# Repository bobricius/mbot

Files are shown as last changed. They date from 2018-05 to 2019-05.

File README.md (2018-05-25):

# mbot

2D actuator move micro robot in X/Y 2D space
Less than 10$ educational platform with micro magnetic robot (mBot), 
only 6 GPIO to move in unlimited X/Y 2D space

Great for physical education for languages like Karel and make 
SKOBAN game or solve acrylic cutted labyrinth. 

My project not violating SRI international patent 
(maybe, I am not patent expert) 

There is differences: 

- I am using another moving track configutation 
- Control is 3-phase unipolar against 4-phase bipolar 
- My manipulator (mBot) use 4 magnets and not levitating 
- For move in one dimension I need only 3x Mosfets connected to any MCU 
(Arduino Atmega328, Stm32, MSP430, ESP XXXX) 
- 6 GPIO to move in X/Y 2D space 
- Moving board can be produced in any fab, it is just only PCB board 8/8mil 
- IT IS CHEAP

PROJECT PAGE

https://hackaday.io/project/154496-2d-actuator-move-micro-robot-in-xy-2d-space

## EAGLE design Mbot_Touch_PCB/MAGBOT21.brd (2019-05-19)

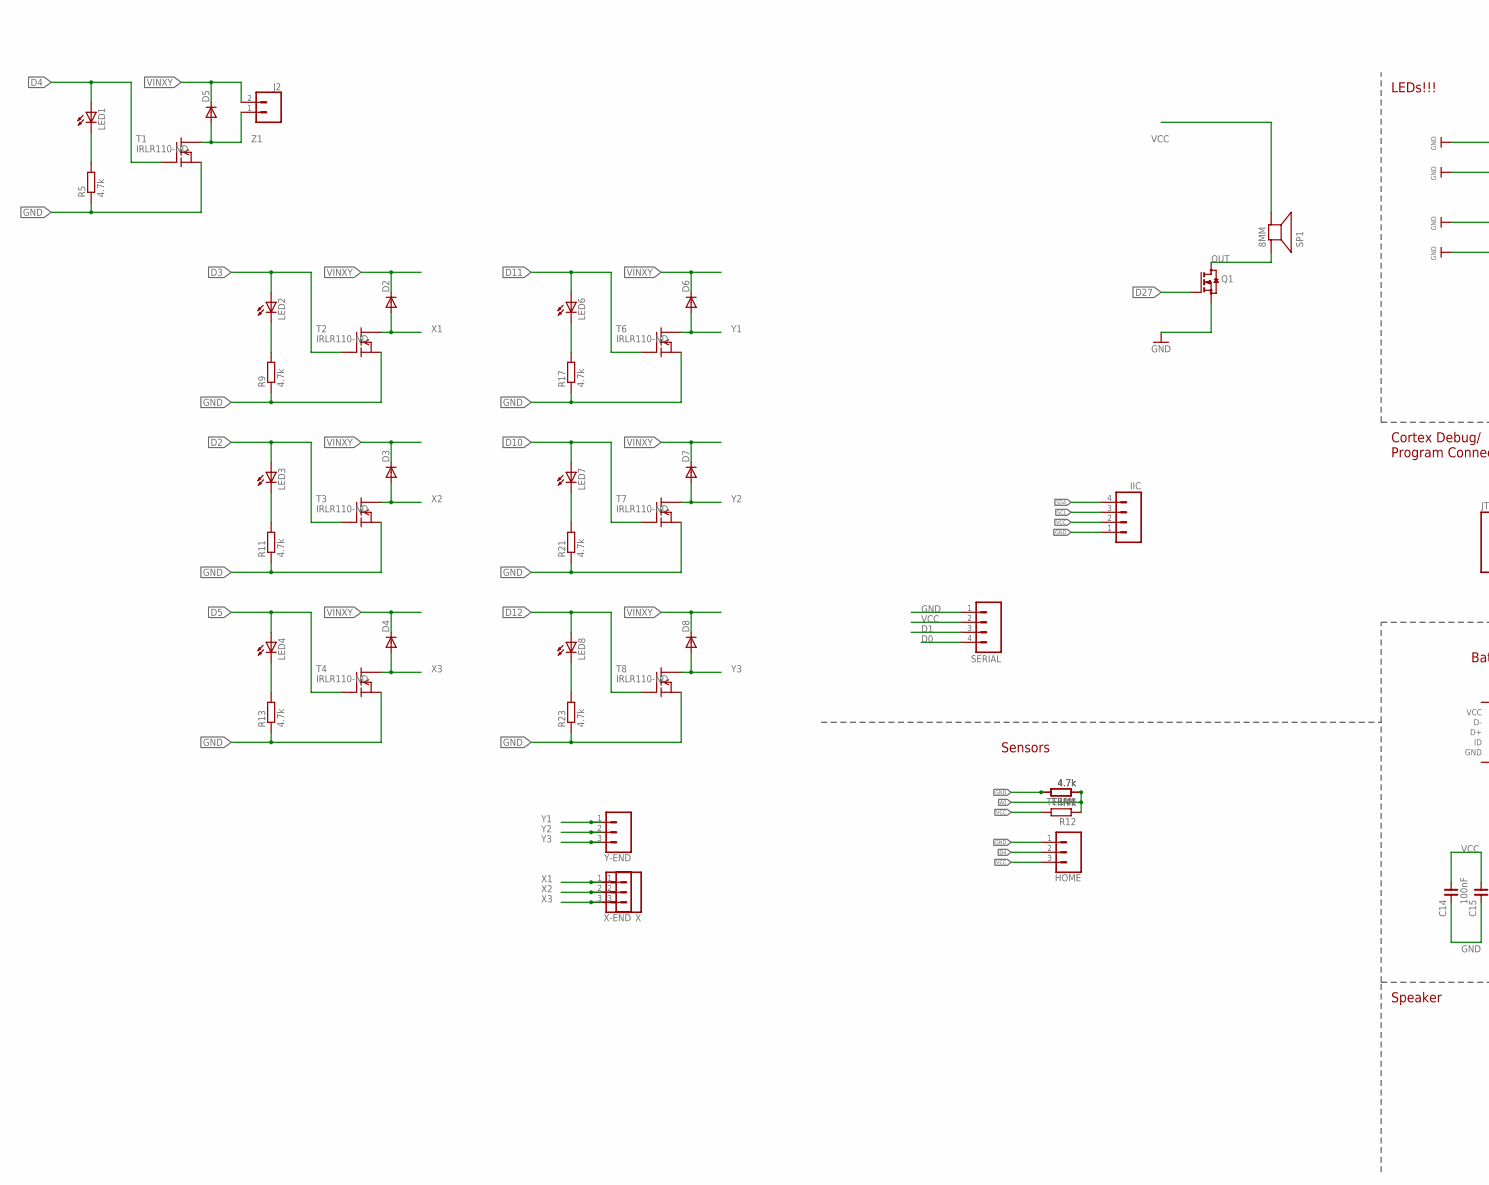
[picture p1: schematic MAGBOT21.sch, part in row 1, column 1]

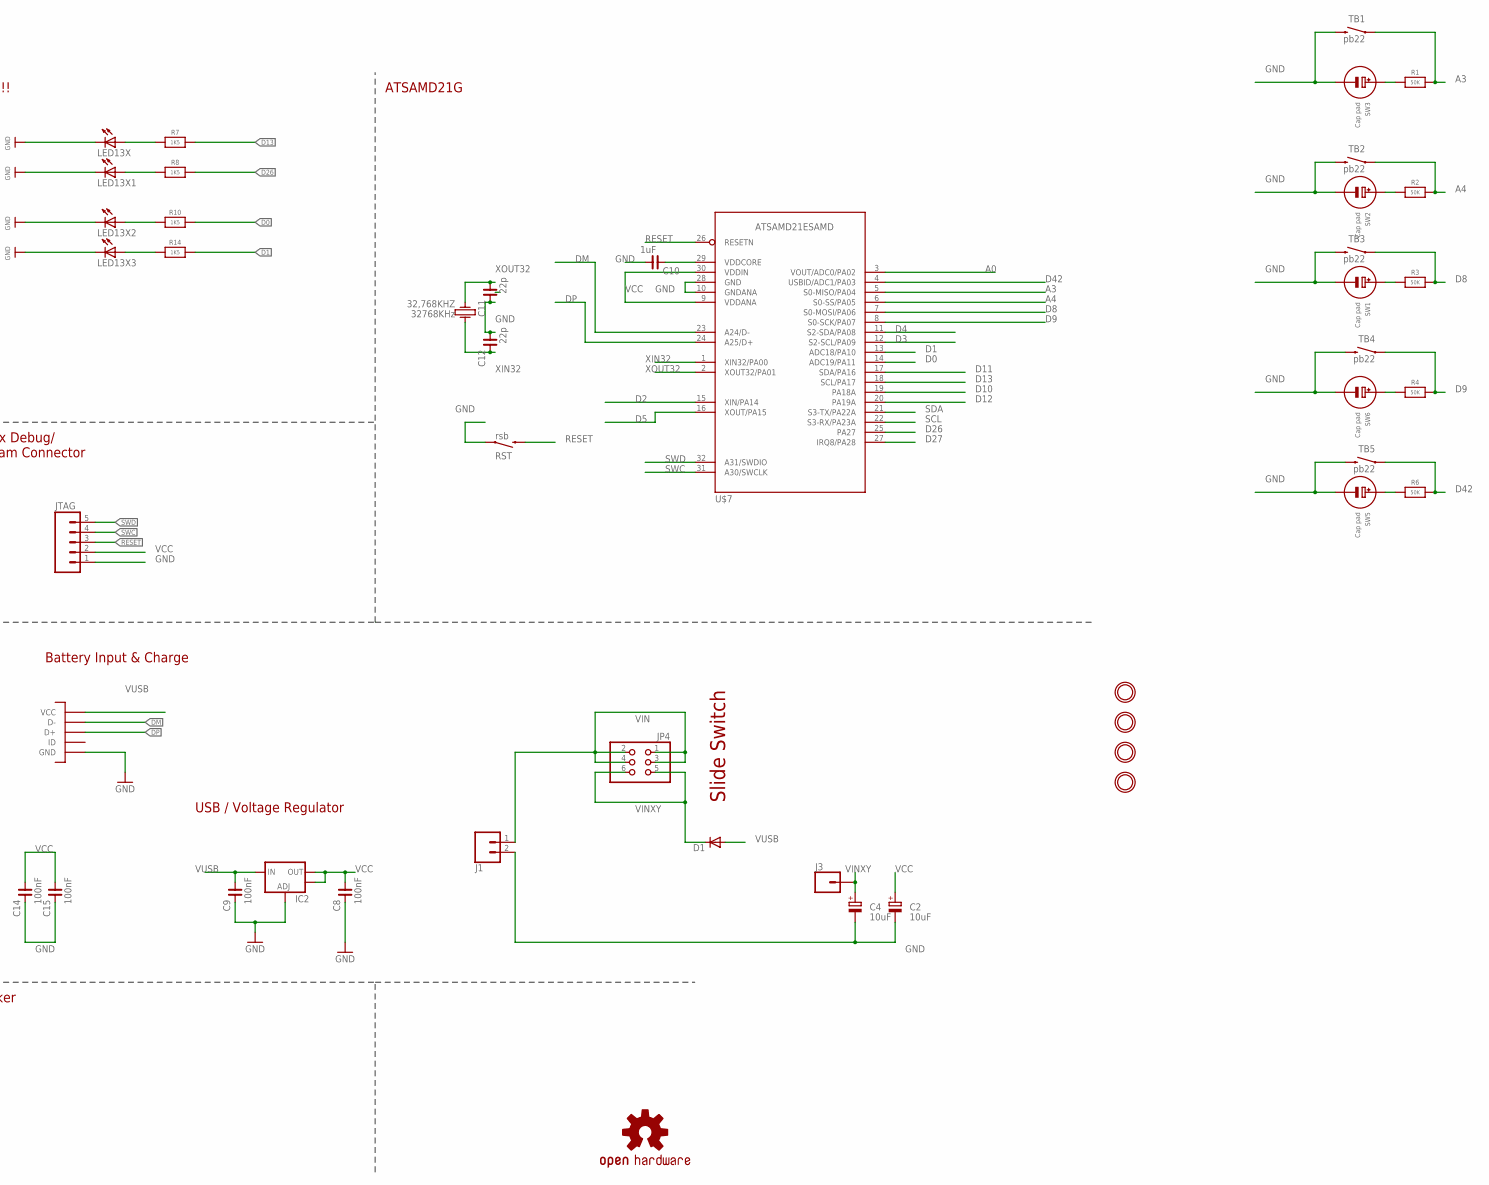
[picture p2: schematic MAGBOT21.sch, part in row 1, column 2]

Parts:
32,768KHZ: 32768KHz; KX-327LT
C2, C4: 10uF; 153CLV-0605
C8, C9: 100nF; C0603
C10: 1uF; C0805
C11, C12: 22p; C0805
C14, C15: 100nF; C0805
D1, D2, D3, D4, D5, D6, D7, D8: DIODE-DO214AC; DO214AC
HOME: CONN_031X03_NO_SILK; 1X03_NO_SILK
IC2: V_REG_LM1117SOT223; SOT223
IIC: M041X04_NO_SILK; 1X04_NO_SILK
J1, J2: CONN_02PTH3; 1X02_LONGPADS
J3: CONN_01PTH_NO_SILK_KIT; 1X01NS_KIT
JP4: PINHD-2X3; 2X03
JTAG: M051.27MM; 1X05-1.27MM
LED1, LED2, LED3, LED4, LED6, LED7, LED8, LED13X, LED13X1: LEDCHIPLED_0805; CHIPLED_0805
LED13X2, LED13X3: LEDCHIPLED_0603; CHIPLED_0603
LOGO3: OSHW-LOGOS; OSHW-LOGO-S
Q1: BSS123; SOT23
R1, R2, R3, R4, R6: 50K; _0805
R5, R9, R11, R12, R13, R17, R21, R23: 4.7k; R0603
R7: 1K5; _0805MP
R8: 1K5; 0603-NO
R10, R14: 1K5; _0603MP
RST: rsb; TACTILE_SWITCH_SMD-3
SERIAL: M041X04_NO_SILK; 1X04_NO_SILK
SP1: 8MM; BUZZER_SMT_5MM
SW1, SW2, SW3, SW5, SW6: Cap pad; CAPTOUCH_SIMPLE_12.5MM
T1, T2, T3, T4, T6, T7, T8: IRLR110-ND; TO252
TB1, TB2, TB3, TB4, TB5: pb22; TACTILE_SWITCH_SMD-3
TERM, TERM1: 4.7k; R0805W
U$3, U$4, U$8, U$10: MOUNTINGHOLE2.0; MOUNTINGHOLE_2.0_PLATED
U$5: MICROUSB; MICRO_B
U$7: ATSAMD21ESAMD; TQFP32-08
X: CONN_031X03_NO_SILK; 1X03_NO_SILK
X-END: CONN_031X03_NO_SILK; 1X03_NO_SILK
Y-END: CONN_031X03_NO_SILK; 1X03_NO_SILK

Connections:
A0: R12.1, TERM.1, TERM1.1, U$7.3 (VOUT/ADC0/PA02)
A3: R1.1, TB1.1, U$7.5 (S0-MISO/PA04)
A4: R2.1, TB2.1, U$7.6 (S0-SS/PA05)
D0: R10.1, SERIAL.4, U$7.14 (ADC19/PA11)
D1: R14.1, SERIAL.3, U$7.13 (ADC18/PA10)
D2: LED3.A, T3.1 (G), U$7.15 (XIN/PA14)
D3: LED2.A, T2.1 (G), U$7.12 (S2-SCL/PA09)
D4: HOME.2, LED1.A, T1.1 (G), U$7.11 (S2-SDA/PA08)
D5: LED4.A, T4.1 (G), U$7.16 (XOUT/PA15)
D8: R3.1, TB3.1, U$7.7 (S0-MOSI/PA06)
D9: R4.1, TB4.1, U$7.8 (S0-SCK/PA07)
D10: LED7.A, T7.1 (G), U$7.19 (PA18A)
D11: LED6.A, T6.1 (G), U$7.17 (SDA/PA16)
D12: LED8.A, T8.1 (G), U$7.20 (PA19A)
D13: R7.1, U$7.18 (SCL/PA17)
D26: R8.1, U$7.25 (PA27)
D27: Q1.1 (G), U$7.27 (IRQ8/PA28)
D42: R6.1, TB5.1, U$7.4 (USBID/ADC1/PA03)
DM: U$5.P2 (D-), U$7.23 (A24/D-)
DP: U$5.P3 (D+), U$7.24 (A25/D+)
GND: C2.-, C4.-, C8.2, C9.2, C10.1, C11.2, C12.1, C14.2, C15.2, HOME.1, IC2.1 (ADJ), IIC.1, J1.2, JTAG.1, LED13X.C, LED13X1.C, LED13X2.C, LED13X3.C, Q1.2 (S), R5.1, R9.1, R11.1, R13.1, R17.1, R21.1, R23.1, RST.1, SERIAL.1, SW1.G (-), SW2.G (-), SW3.G (-), SW5.G (-), SW6.G (-), T1.2 (S), T2.2 (S), T3.2 (S), T4.2 (S), T6.2 (S), T7.2 (S), T8.2 (S), TB1.4 (2), TB2.4 (2), TB3.4 (2), TB4.4 (2), TB5.4 (2), TERM.2, TERM1.2, U$5.GND1 (GND), U$5.GND2 (GND), U$5.GND3 (GND), U$5.GND4 (GND), U$5.GND7 (GND), U$5.GND8 (GND), U$5.P5 (GND), U$7.10 (GNDANA), U$7.28 (GND)
unnamed: R6.2, SW5.E (+)
unnamed: R4.2, SW6.E (+)
unnamed: R3.2, SW1.E (+)
unnamed: R2.2, SW2.E (+)
unnamed: R1.2, SW3.E (+)
unnamed: LED13X1.A, R8.2
unnamed: LED2.C, R9.2
unnamed: LED6.C, R17.2
unnamed: C10.2, U$7.29 (VDDCORE)
unnamed: LED3.C, R11.2
unnamed: LED7.C, R21.2
unnamed: LED4.C, R13.2
unnamed: LED8.C, R23.2
unnamed: LED13X.A, R7.2
unnamed: LED1.C, R5.2
unnamed: LED13X2.A, R10.2
unnamed: LED13X3.A, R14.2
OUT: Q1.3 (D), SP1.+
RESET: JTAG.3, RST.4 (2), U$7.26 (RESETN)
SCL: IIC.3, U$7.22 (S3-RX/PA23A)
SDA: IIC.4, U$7.21 (S3-TX/PA22A)
SWC: JTAG.4, U$7.31 (A30/SWCLK)
SWD: JTAG.5, U$7.32 (A31/SWDIO)
VCC: C2.+, C8.1, C14.1, C15.1, HOME.3, IC2.2 (OUT), IC2.4 (OUT), IIC.2, JTAG.2, R12.2, SERIAL.2, SP1.-, U$7.9 (VDDANA), U$7.30 (VDDIN)
VIN: J1.1, JP4.1, JP4.2, JP4.3, JP4.4
VINXY: C4.+, D1.C, D2.C, D3.C, D4.C, D5.C, D6.C, D7.C, D8.C, J2.2, J3.1, JP4.5, JP4.6
VUSB: C9.1, D1.A, IC2.3 (IN), U$5.P1 (VCC)
X1: D2.A, T2.3 (D), X.1, X-END.1
X2: D3.A, T3.3 (D), X.2, X-END.2
X3: D4.A, T4.3 (D), X.3, X-END.3
XIN32: 32,768KHZ.1, C12.2, U$7.1 (XIN32/PA00)
XOUT32: 32,768KHZ.4, C11.1, U$7.2 (XOUT32/PA01)
Y1: D6.A, T6.3 (D), Y-END.1
Y2: D7.A, T7.3 (D), Y-END.2
Y3: D8.A, T8.3 (D), Y-END.3
Z1: D5.A, J2.1, T1.3 (D)

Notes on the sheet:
USB / Voltage Regulator
LEDs!!!
Cortex Debug/ Program Connector
Sensors
ATSAMD21G
Battery Input & Charge
Speaker
Slide Switch

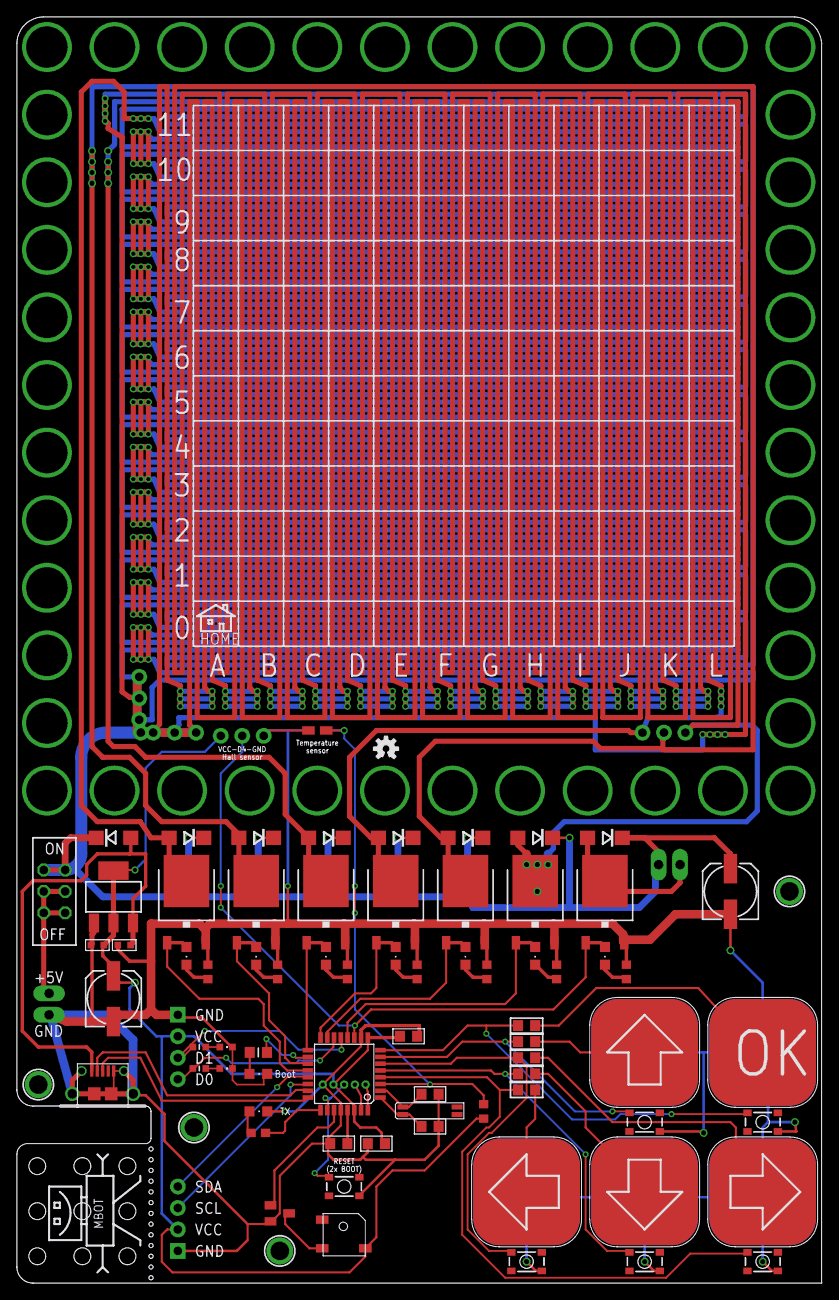
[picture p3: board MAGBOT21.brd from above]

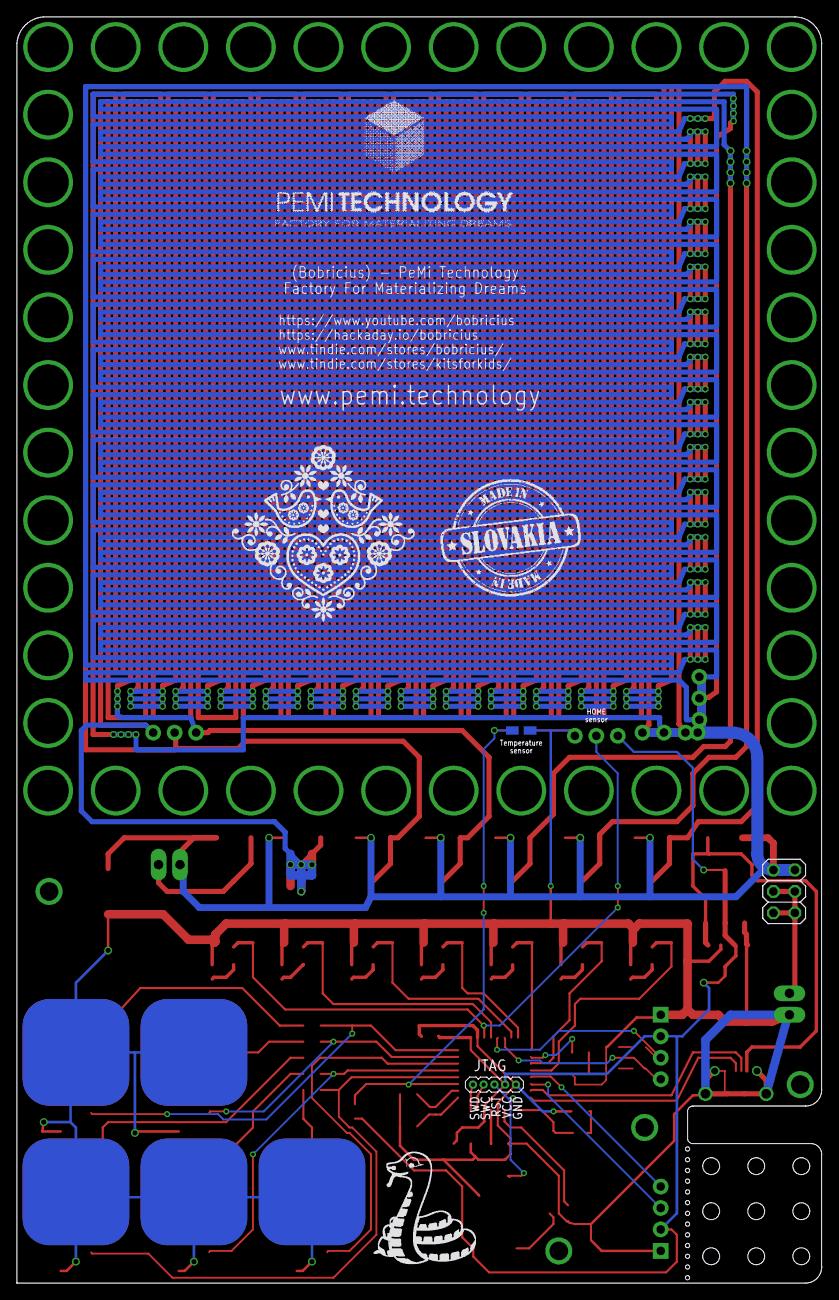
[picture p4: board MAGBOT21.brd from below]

Board: 2 copper layers, 95.2 x 149.9 mm, 87 parts (4 on the bottom side), 57 nets.

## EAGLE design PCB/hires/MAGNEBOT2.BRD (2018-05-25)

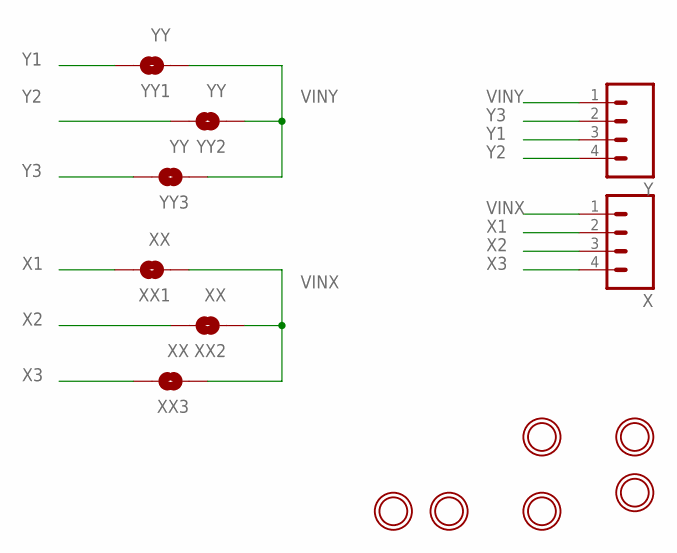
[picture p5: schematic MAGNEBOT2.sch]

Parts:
U$1, U$2, U$3, U$4, U$5, U$10: MOUNTINGHOLE2.0; MOUNTINGHOLE_2.0_PLATED
X: M04PTH; 1X04
XX1, XX2, XX3: XX; SJ_2S-TRACE
Y: M04PTH; 1X04
YY1, YY2, YY3: YY; SJ_2S-TRACE

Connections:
VINX: X.1, XX1.1, XX2.1, XX3.1
VINY: Y.1, YY1.1, YY2.1, YY3.1
X1: X.2, XX1.2
X2: X.3, XX2.2
X3: X.4, XX3.2
Y1: Y.3, YY1.2
Y2: Y.4, YY2.2
Y3: Y.2, YY3.2

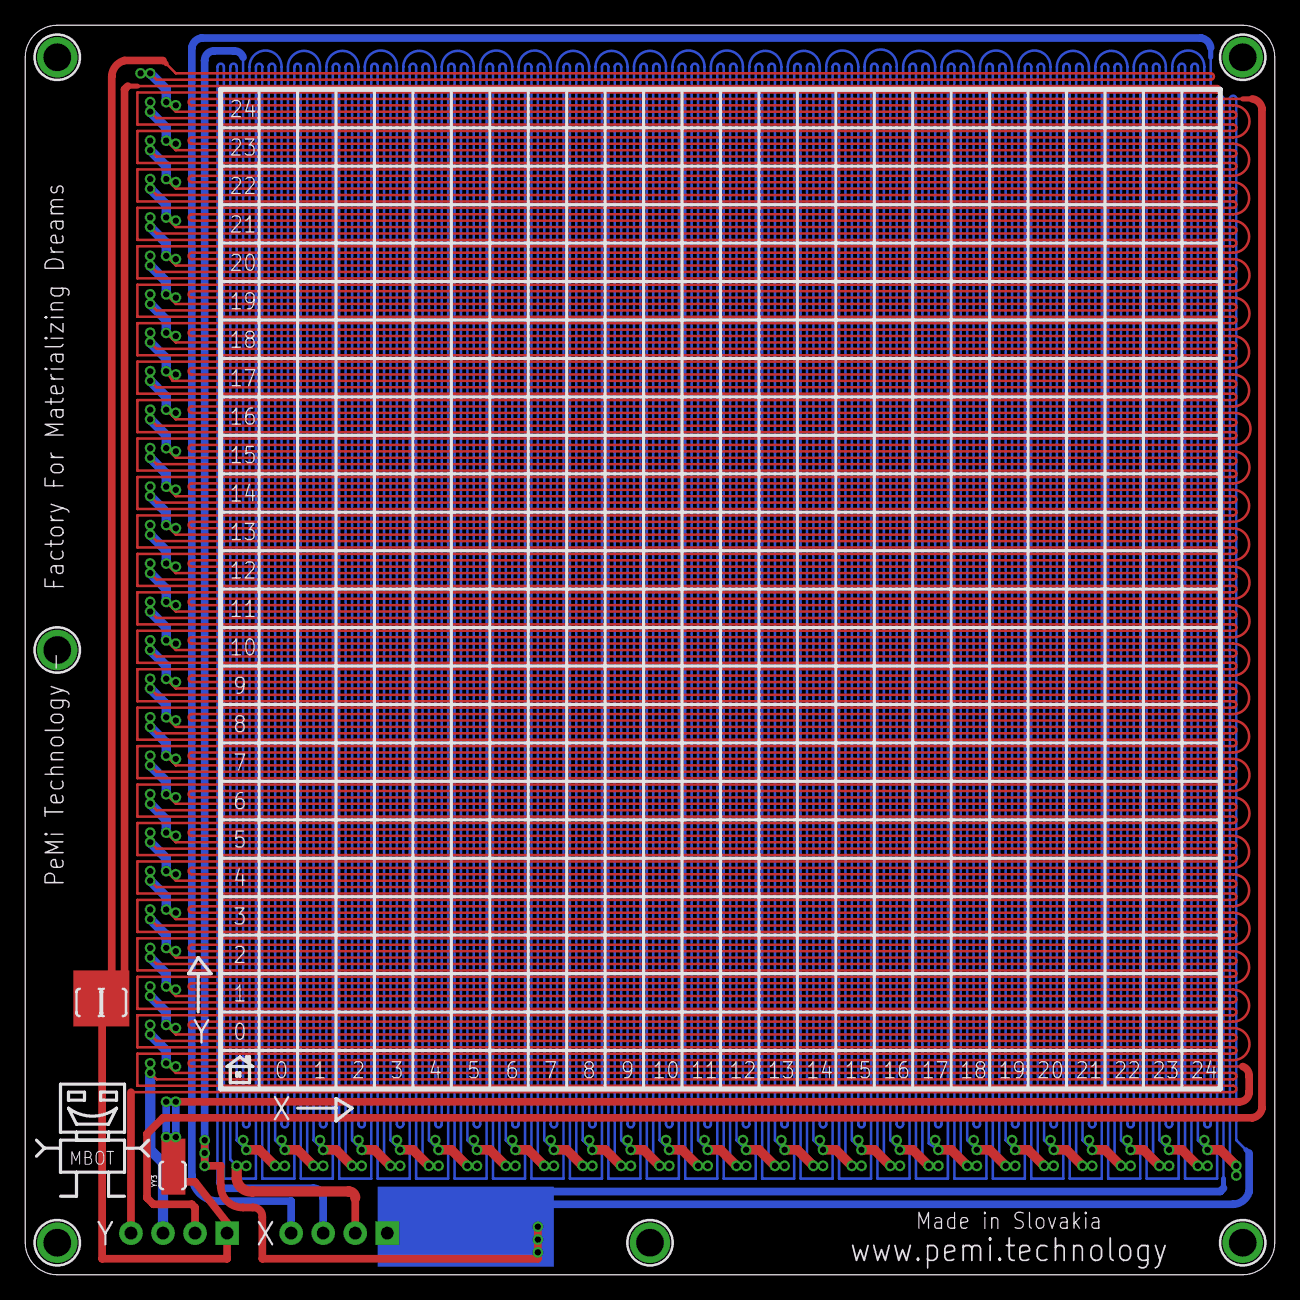
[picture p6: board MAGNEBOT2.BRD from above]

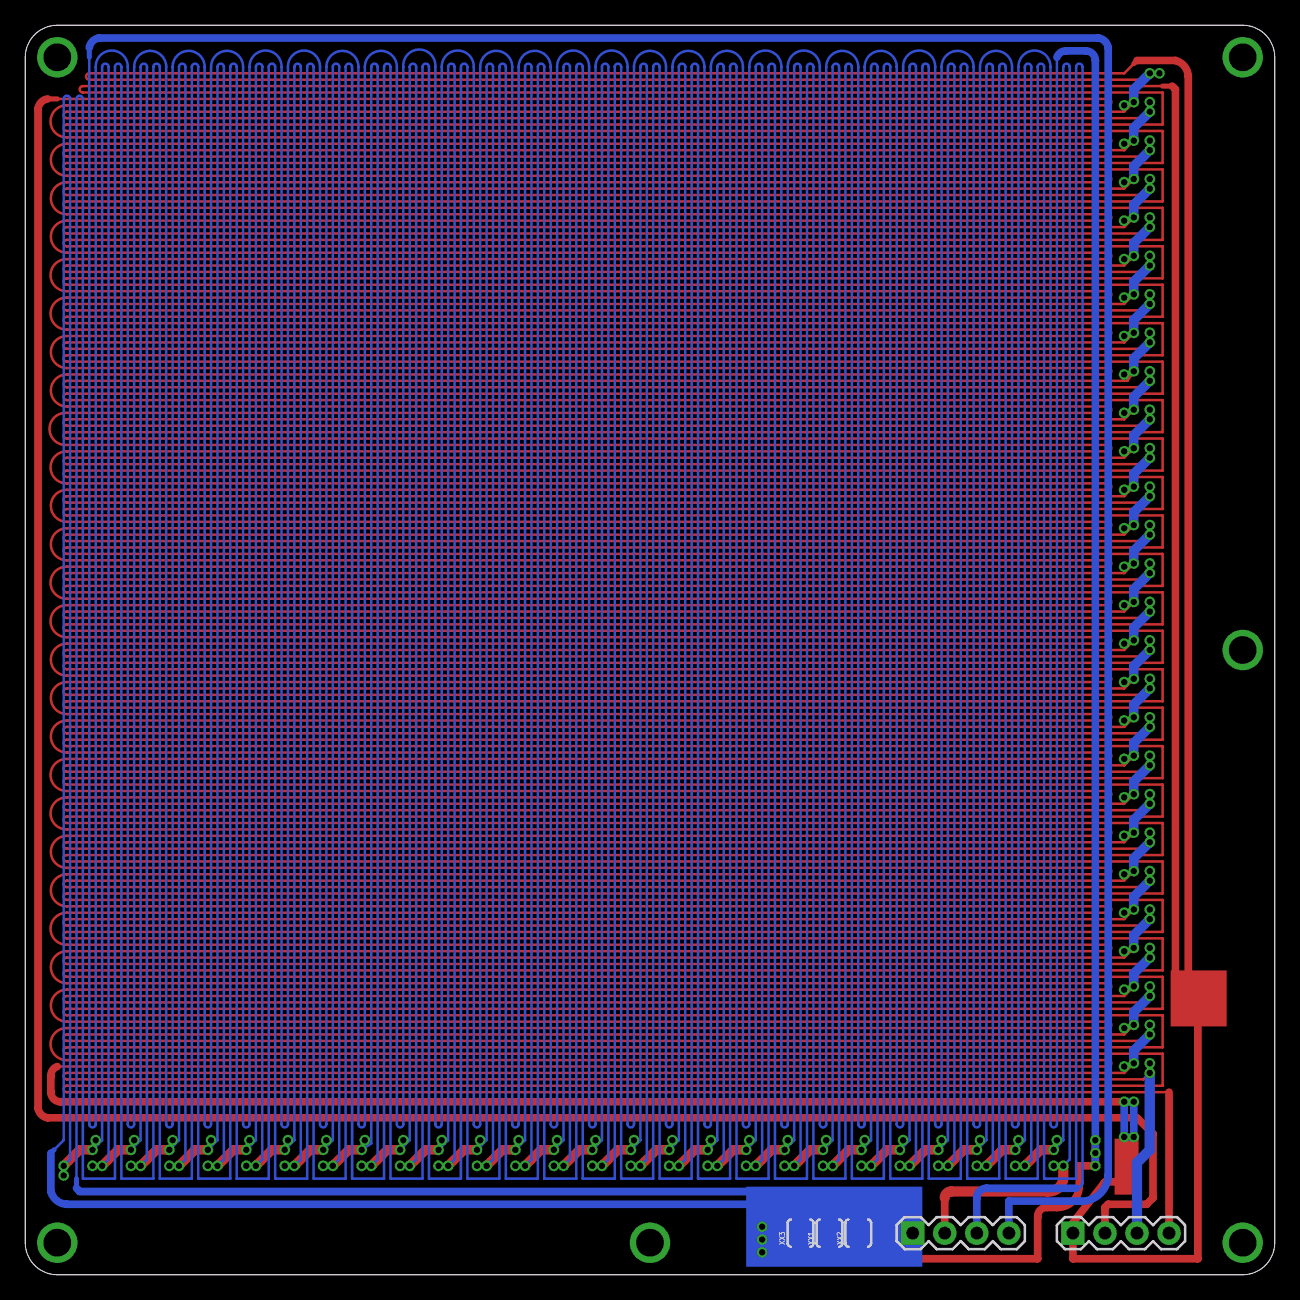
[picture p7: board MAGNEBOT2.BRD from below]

Board: 2 copper layers, 99.1 x 99.1 mm, 14 parts (5 on the bottom side), 8 nets.

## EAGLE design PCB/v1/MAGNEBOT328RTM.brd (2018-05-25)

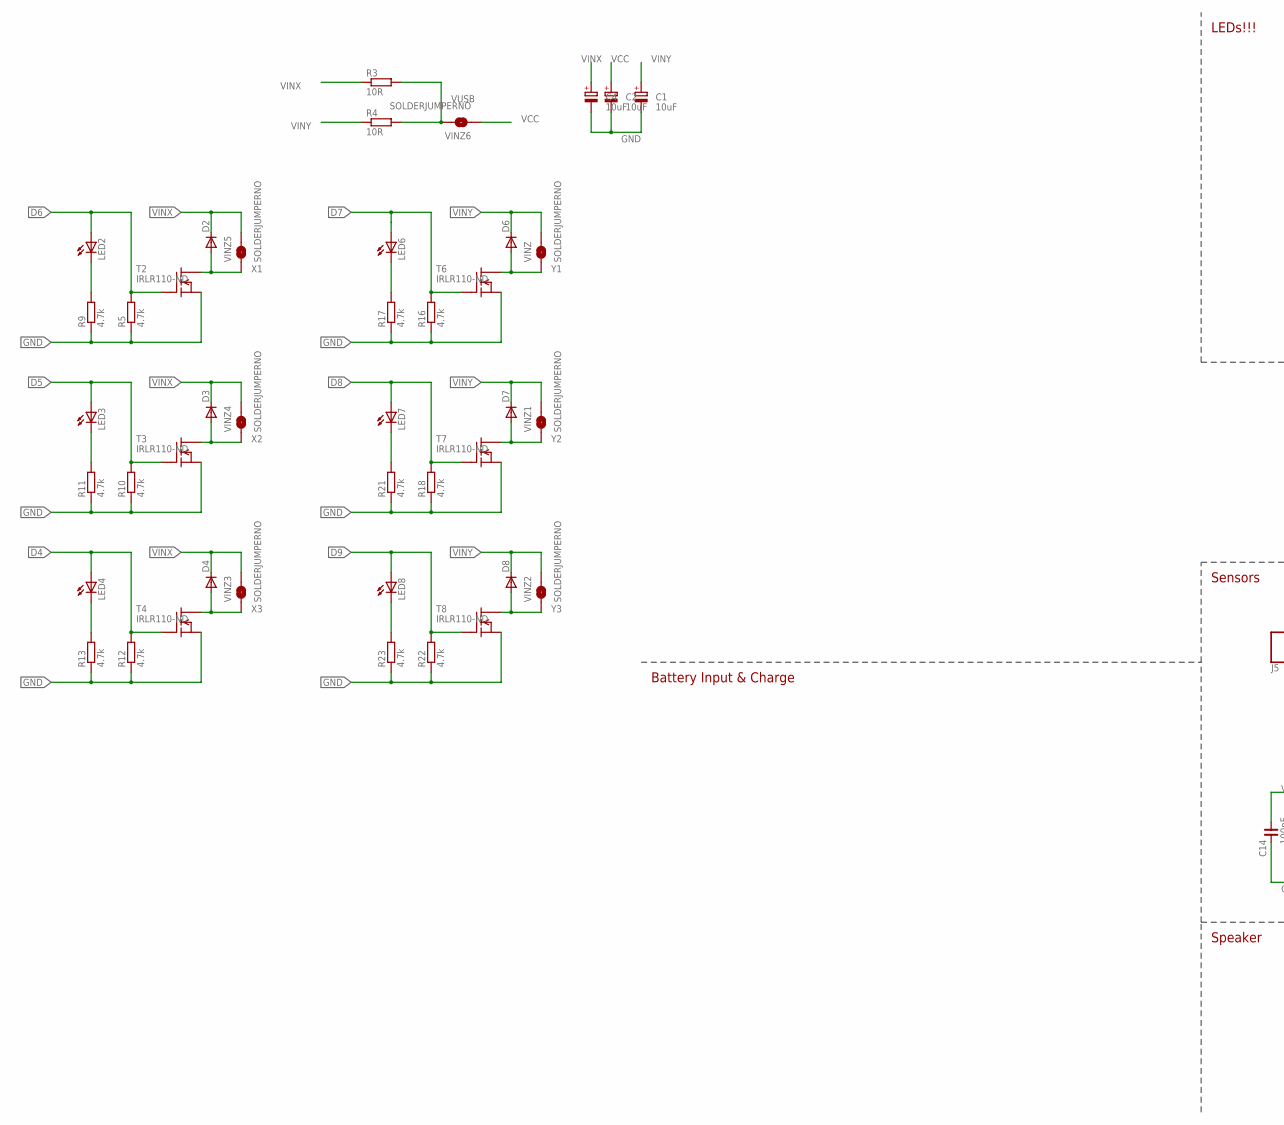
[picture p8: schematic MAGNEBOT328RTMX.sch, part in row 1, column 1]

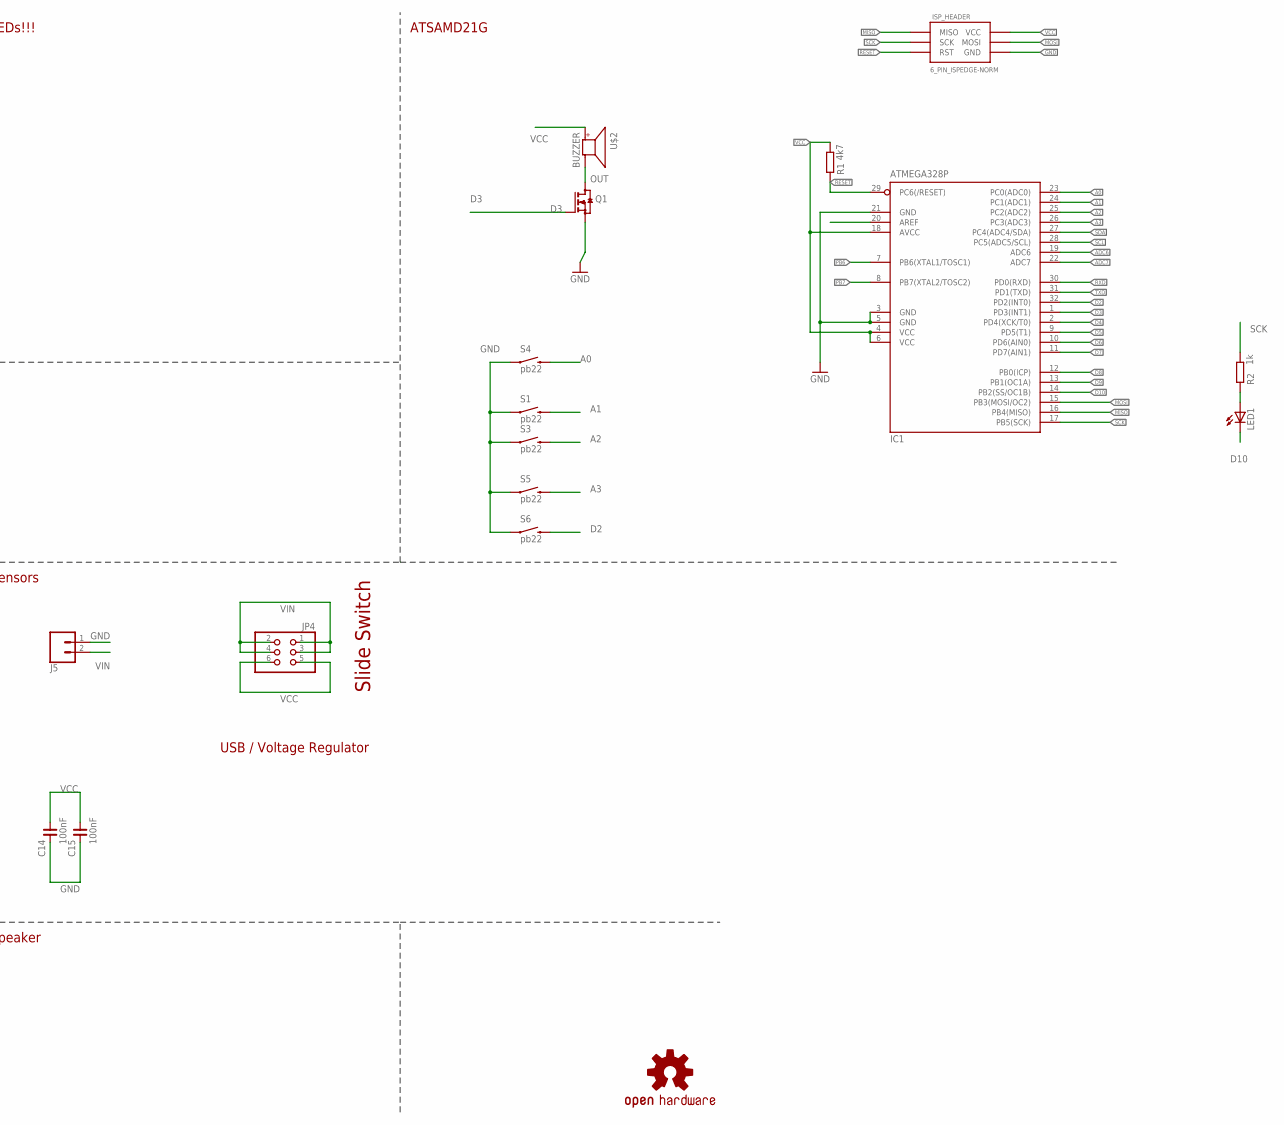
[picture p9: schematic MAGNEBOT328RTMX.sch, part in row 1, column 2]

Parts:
C1, C2, C4: 10uF; E2,5-7
C14, C15: 100nF; C0603
D2, D3, D4, D6, D7, D8: DIODE-DO214AC; DO214AC
IC1: ATMEGA328P; TQFP32-08
ISP_HEADER: 6_PIN_ISPEDGE-NORM; 6_PIN_EDGE
J5: CONN_02PTH3; 1X02_LONGPADS
JP4: PINHD-2X3; 2X03
LED1: LEDCHIPLED_0603; CHIPLED_0603
LED2: LEDCHIP-LED0805; CHIP-LED0805
LED3, LED4, LED6, LED7, LED8: LEDCHIPLED_0805; CHIPLED_0805
LOGO3: OSHW-LOGOS; OSHW-LOGO-S
Q1: BSS123; SOT23
R1: 4k7; R0603
R2: 1k; R0603
R3, R4: 10R; 0309/12
R5, R9, R10, R11, R12, R13, R16, R17, R18, R21, R22, R23: 4.7k; R0603
S1, S3, S4, S5, S6: pb22; TACTILE-PTH
T2, T3, T4, T6, T7, T8: IRLR110-ND; TO252
U$2: BUZZER; SMT-8585-BUZZER
VINZ, VINZ1, VINZ2, VINZ3, VINZ4, VINZ5, VINZ6: SOLDERJUMPERNO; SJ_2S-NO

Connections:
A0: IC1.23 (PC0(ADC0)), S4.3 (2)
A1: IC1.24 (PC1(ADC1)), S1.3 (2)
A2: IC1.25 (PC2(ADC2)), S3.3 (2)
A3: IC1.26 (PC3(ADC3)), S5.3 (2)
ADC6: IC1.19 (ADC6)
ADC7: IC1.22 (ADC7)
AREF: IC1.20 (AREF)
D2: IC1.32 (PD2(INT0)), S6.3 (2)
D3: IC1.1 (PD3(INT1)), Q1.1 (G)
D4: IC1.2 (PD4(XCK/T0)), LED4.A, R12.2, T4.1 (G)
D5: IC1.9 (PD5(T1)), LED3.A, R10.2, T3.1 (G)
D6: IC1.10 (PD6(AIN0)), LED2.A, R5.2, T2.1 (G)
D7: IC1.11 (PD7(AIN1)), LED6.A, R16.2, T6.1 (G)
D8: IC1.12 (PB0(ICP)), LED7.A, R18.2, T7.1 (G)
D9: IC1.13 (PB1(OC1A)), LED8.A, R22.2, T8.1 (G)
D10: IC1.14 (PB2(SS/OC1B)), LED1.C
GND: C1.-, C2.-, C4.-, C14.2, C15.2, IC1.3 (GND), IC1.5 (GND), IC1.21 (GND), ISP_HEADER.6 (GND), J5.1, Q1.2 (S), R5.1, R9.1, R10.1, R11.1, R12.1, R13.1, R16.1, R17.1, R18.1, R21.1, R22.1, R23.1, S1.1, S3.1, S4.1, S5.1, S6.1, T2.2 (S), T3.2 (S), T4.2 (S), T6.2 (S), T7.2 (S), T8.2 (S)
MISO: IC1.16 (PB4(MISO)), ISP_HEADER.1 (MISO)
MOSI: IC1.15 (PB3(MOSI/OC2)), ISP_HEADER.4 (MOSI)
unnamed: LED1.A, R2.2
unnamed: LED2.C, R9.2
unnamed: LED6.C, R17.2
unnamed: LED3.C, R11.2
unnamed: LED7.C, R21.2
unnamed: LED4.C, R13.2
unnamed: LED8.C, R23.2
OUT: Q1.3 (D), U$2.-
PB6: IC1.7 (PB6(XTAL1/TOSC1))
PB7: IC1.8 (PB7(XTAL2/TOSC2))
RESET: IC1.29 (PC6(/RESET)), ISP_HEADER.5 (RST), R1.2
RXD: IC1.30 (PD0(RXD))
SCK: IC1.17 (PB5(SCK)), ISP_HEADER.3 (SCK), R2.1
SCL: IC1.28 (PC5(ADC5/SCL))
SDA: IC1.27 (PC4(ADC4/SDA))
TXD: IC1.31 (PD1(TXD))
VCC: C2.+, C14.1, C15.1, IC1.4 (VCC), IC1.6 (VCC), IC1.18 (AVCC), ISP_HEADER.2 (VCC), JP4.5, JP4.6, R1.1, U$2.+, VINZ6.1
VIN: J5.2, JP4.1, JP4.2, JP4.3, JP4.4
VINX: C4.+, D2.C, D3.C, D4.C, R3.1, VINZ3.2, VINZ4.2, VINZ5.2
VINY: C1.+, D6.C, D7.C, D8.C, R4.1, VINZ.2, VINZ1.2, VINZ2.2
VUSB: R3.2, R4.2, VINZ6.2
X1: D2.A, T2.3 (D), VINZ5.1
X2: D3.A, T3.3 (D), VINZ4.1
X3: D4.A, T4.3 (D), VINZ3.1
Y1: D6.A, T6.3 (D), VINZ.1
Y2: D7.A, T7.3 (D), VINZ1.1
Y3: D8.A, T8.3 (D), VINZ2.1

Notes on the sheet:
USB / Voltage Regulator
LEDs!!!
Sensors
ATSAMD21G
Battery Input & Charge
Speaker
Slide Switch

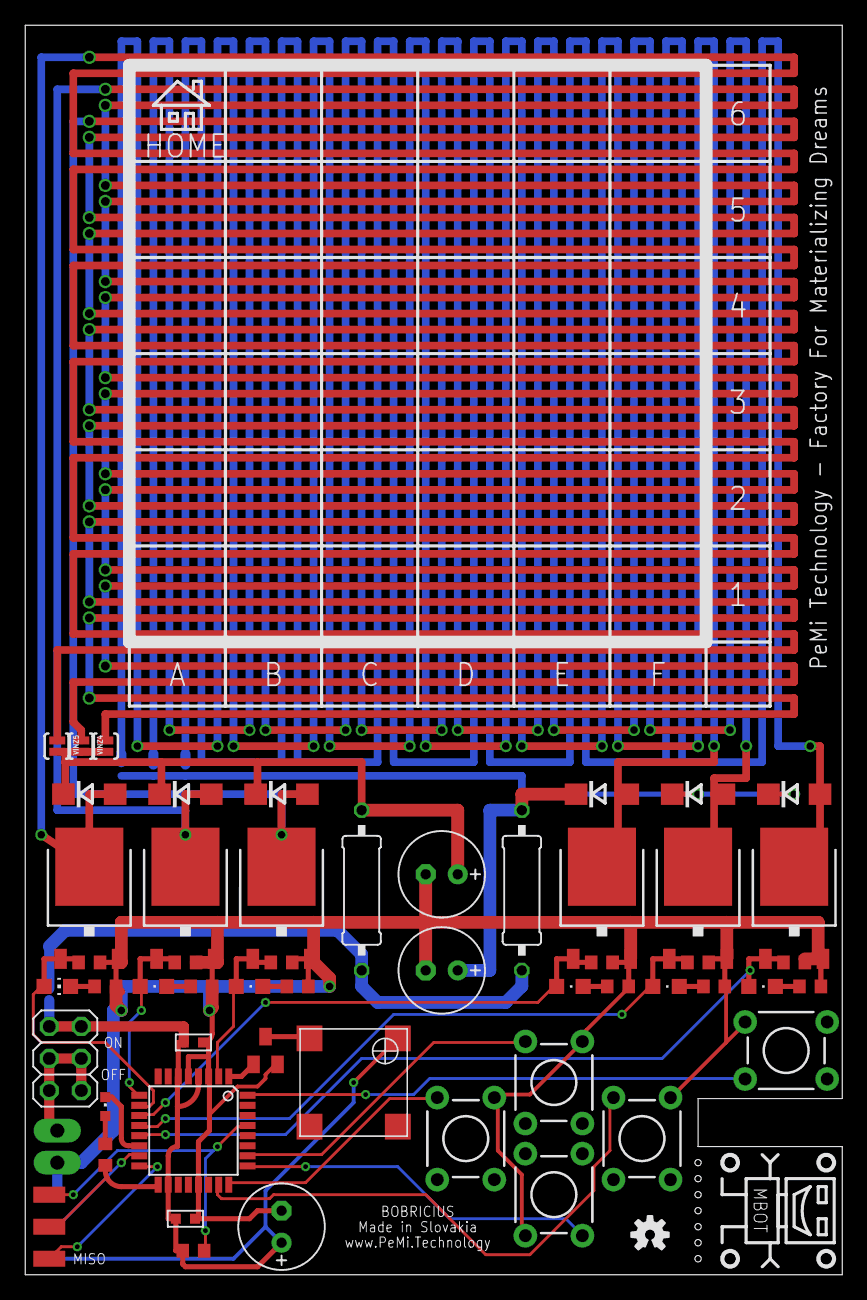
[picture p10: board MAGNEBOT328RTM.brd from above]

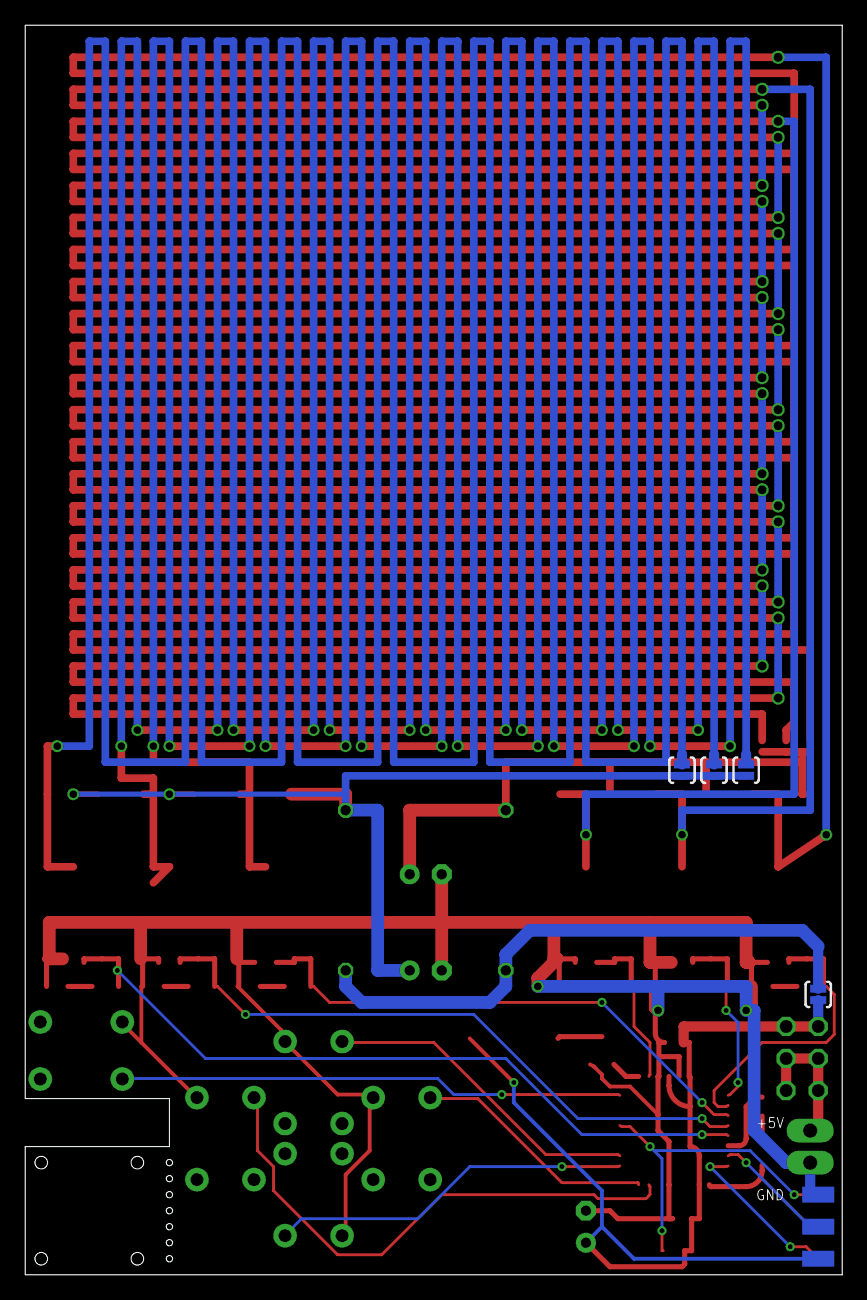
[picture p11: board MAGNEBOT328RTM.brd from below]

Board: 2 copper layers, 64.8 x 99.1 mm, 59 parts (4 on the bottom side), 37 nets.

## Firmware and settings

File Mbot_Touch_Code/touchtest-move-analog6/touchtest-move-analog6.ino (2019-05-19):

#include "Adafruit_FreeTouch.h"

Adafruit_FreeTouch qt_up = Adafruit_FreeTouch(8, OVERSAMPLE_4, RESISTOR_50K, FREQ_MODE_NONE);
Adafruit_FreeTouch qt_down = Adafruit_FreeTouch(A3, OVERSAMPLE_4, RESISTOR_50K, FREQ_MODE_NONE);
Adafruit_FreeTouch qt_left = Adafruit_FreeTouch(A4, OVERSAMPLE_4, RESISTOR_50K, FREQ_MODE_NONE);
Adafruit_FreeTouch qt_right = Adafruit_FreeTouch(42, OVERSAMPLE_4, RESISTOR_50K, FREQ_MODE_NONE);
Adafruit_FreeTouch qt_play = Adafruit_FreeTouch(9, OVERSAMPLE_4, RESISTOR_50K, FREQ_MODE_NONE);

#define X1   3
#define X2   2
#define X3   5

#define Y1   12
#define Y2   10
#define Y3   11

#define COIL   4
#define FULLPOWER   255
#define KEEPTRACK   30

#define XLED   0
#define YLED   1
#define PLAYLED   13



#define SPEED  15

int xpos = 1000;
int ypos = 1000;



void setup() {
//  SerialUSB.begin(115200);
  
//  while (!SerialUSB);
//  SerialUSB.println("FreeTouch test");
  // initialize digital pin LED_BUILTIN as an output.
  pinMode(X1, OUTPUT);
  pinMode(X2, OUTPUT);
  pinMode(X3, OUTPUT);

  pinMode(XLED, OUTPUT);
  pinMode(YLED, OUTPUT);
  pinMode(PLAYLED, OUTPUT);

  digitalWrite(XLED, LOW);
  digitalWrite(YLED, LOW);
  digitalWrite(PLAYLED, LOW);
  
  digitalWrite(X1, LOW);
  digitalWrite(X2, LOW);
  digitalWrite(X3, LOW);

  pinMode(Y1, OUTPUT);
  pinMode(Y2, OUTPUT);
  pinMode(Y3, OUTPUT);
  digitalWrite(Y1, LOW);
  digitalWrite(Y2, LOW);
  digitalWrite(Y3, LOW);

  pinMode(COIL, OUTPUT);
  digitalWrite(COIL, LOW);

qt_up.begin(); 
qt_down.begin(); 
qt_left.begin();  
qt_right.begin();  
qt_play.begin(); 

   analogWriteResolution(8) ;
}



void loop() {
if (qt_down.measure()>850) down_step(1); 
if (qt_up.measure()>850) up_step(1); 
if (qt_left.measure()>850) left_step(1); 
if (qt_right.measure()>850) right_step(1); 
if (qt_play.measure()>850) play(); 
  
}

void play ()
{
  digitalWrite(PLAYLED, HIGH); 
right_step(20);
down_step(20);
left_step(20);
up_step(20);             

right_step(10);
down_step(10);
left_step(10);
up_step(10);   
  digitalWrite(PLAYLED, LOW);  
}


void x_step (int xx, char pwr)
{
switch (xx%6){
 case 0:
   analogWrite(X1, pwr); 
  break;
 case 1:
   analogWrite(X1, pwr);
   analogWrite(X2, pwr);  
  break;
 case 2:
   analogWrite(X2, pwr);
  break;
 case 3:
   analogWrite(X2, pwr);
   analogWrite(X3, pwr); 
  break;
 case 4:
   analogWrite(X3, pwr); 
  break;
 case 5:
   analogWrite(X3, pwr);
   analogWrite(X1, pwr);   
  break;     
}
}

void y_step (int yy, char pwr)
{
switch (yy%6){
 case 0:
   analogWrite(Y1, pwr); 
  break;
 case 1:
   analogWrite(Y1, pwr);
   analogWrite(Y2, pwr);  
  break;
 case 2:
   analogWrite(Y2, pwr);
  break;
 case 3:
   analogWrite(Y2, pwr);
   analogWrite(Y3, pwr); 
  break;
 case 4:
   analogWrite(Y3, pwr); 
  break;
 case 5:
   analogWrite(Y3, pwr);
   analogWrite(Y1, pwr);   
  break;     
}
}

void right_step (int i){
  for (int a = 0 ; a < i;  a++) {
  xpos++;
  y_step (ypos,KEEPTRACK);  
  x_step (xpos,FULLPOWER);
  delay (SPEED);
  off_all() ;  
//  delay (SPEED); 
  }
  
}

void left_step (int i){
  for (int a = 0 ; a < i;  a++) {
  xpos--;
  y_step (ypos,KEEPTRACK);  
  x_step (xpos,FULLPOWER);
  delay (SPEED);
  off_all() ;  
//  delay (SPEED);
  } 

}


void down_step (int i)
{
    digitalWrite(YLED, HIGH); 
  for (int a = 0 ; a < i;  a++) {
  ypos--;
  y_step (ypos,FULLPOWER);  
  x_step (xpos,KEEPTRACK);
  delay (SPEED*2);
  off_all() ;  
  } 
    digitalWrite(YLED, LOW); 
}

void up_step (int i)
{
    digitalWrite(XLED, HIGH); 
  for (int a = 0 ; a < i;  a++) {
  ypos++;
  y_step (ypos,FULLPOWER);  
  x_step (xpos,KEEPTRACK);
  delay (SPEED*2);
  off_all() ;  
//  delay (SPEED);
  } 
   digitalWrite(XLED, LOW); 
}

void off_all ()
{
  analogWrite(X1, 0);
  analogWrite(X2, 0);
  analogWrite(X3, 0);  
  analogWrite(Y1, 0);
  analogWrite(Y2, 0);
  analogWrite(Y3, 0);
}

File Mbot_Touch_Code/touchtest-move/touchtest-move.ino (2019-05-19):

#include "Adafruit_FreeTouch.h"

Adafruit_FreeTouch qt_up = Adafruit_FreeTouch(8, OVERSAMPLE_4, RESISTOR_50K, FREQ_MODE_NONE);
Adafruit_FreeTouch qt_down = Adafruit_FreeTouch(A3, OVERSAMPLE_4, RESISTOR_50K, FREQ_MODE_NONE);
Adafruit_FreeTouch qt_left = Adafruit_FreeTouch(A4, OVERSAMPLE_4, RESISTOR_50K, FREQ_MODE_NONE);
Adafruit_FreeTouch qt_right = Adafruit_FreeTouch(42, OVERSAMPLE_4, RESISTOR_50K, FREQ_MODE_NONE);
Adafruit_FreeTouch qt_play = Adafruit_FreeTouch(9, OVERSAMPLE_4, RESISTOR_50K, FREQ_MODE_NONE);

#define X1   3
#define X2   2
#define X3   5

#define Y1   12
#define Y2   10
#define Y3   11

#define COIL   4

#define SPEED   40

int xpos = 1000;
int ypos = 1000;



void setup() {
  SerialUSB.begin(115200);
  
//  while (!SerialUSB);
  SerialUSB.println("FreeTouch test");
  // initialize digital pin LED_BUILTIN as an output.
  pinMode(X1, OUTPUT);
  pinMode(X2, OUTPUT);
  pinMode(X3, OUTPUT);
  digitalWrite(X1, LOW);
  digitalWrite(X2, LOW);
  digitalWrite(X3, LOW);

  pinMode(Y1, OUTPUT);
  pinMode(Y2, OUTPUT);
  pinMode(Y3, OUTPUT);
  digitalWrite(Y1, LOW);
  digitalWrite(Y2, LOW);
  digitalWrite(Y3, LOW);

  pinMode(COIL, OUTPUT);
  digitalWrite(COIL, LOW);

  if (! qt_up.begin())  
    SerialUSB.println("Failed to begin qt on pin 1");
  if (! qt_down.begin())  
    SerialUSB.println("Failed to begin qt on pin 2");
  if (! qt_left.begin())  
    SerialUSB.println("Failed to begin qt on pin 3");
  if (! qt_right.begin())  
    SerialUSB.println("Failed to begin qt on pin 4");
  if (! qt_play.begin())  
    SerialUSB.println("Failed to begin qt on pin 5");

    
}



void loop() {
  int counter, result = 0;
  
  // DIY
//  SerialUSB.println("\n*************************************");
//
//  counter = millis();
//  result = qt_1.measure(); 
//  SerialUSB.print("QT 1: "); SerialUSB.print(result);
//  SerialUSB.print(" (");  SerialUSB.print(millis() - counter); SerialUSB.println(" ms)");
//
//  counter = millis();
//  result = qt_2.measure(); 
//  SerialUSB.print("QT 2: "); SerialUSB.print(result);
//  SerialUSB.print(" (");  SerialUSB.print(millis() - counter); SerialUSB.println(" ms)");
//
//  counter = millis();
//  result = qt_3.measure(); 
//  SerialUSB.print("QT 3: "); SerialUSB.print(result);
//  SerialUSB.print(" (");  SerialUSB.print(millis() - counter); SerialUSB.println(" ms)");
//  
//  counter = millis();
//  result = qt_4.measure(); 
//  SerialUSB.print("QT 4: "); SerialUSB.print(result);
//  SerialUSB.print(" (");  SerialUSB.print(millis() - counter); SerialUSB.println(" ms)");
//
//  result = qt_5.measure(); 
//  SerialUSB.print("QT 5: "); SerialUSB.print(result);
//  SerialUSB.print(" (");  SerialUSB.print(millis() - counter); SerialUSB.println(" ms)");
//  
//  delay(200);


if (qt_down.measure()>850) down_step(); 
if (qt_up.measure()>850) up_step(); 
if (qt_left.measure()>850) left_step(); 
if (qt_right.measure()>850) right_step(); 
if (qt_play.measure()>850) play(); 
  
}

void play ()
{

  digitalWrite(COIL, HIGH); 

             
  digitalWrite(COIL, LOW);  
}


void x_step (int xx)
{
switch (xx%3){
 case 0:
   digitalWrite(X1, HIGH); 
  break;
 case 1:
   digitalWrite(X2, HIGH); 
  break;
 case 2:
   digitalWrite(X3, HIGH);
  break;    
}
}

void y_step (int yy)
{
switch (yy%3){
 case 0:
   digitalWrite(Y1, HIGH); 
  break;
 case 1:
   digitalWrite(Y2, HIGH); 
  break;
 case 2:
   digitalWrite(Y3, HIGH);
  break;    
}
}

void right_step (){
  xpos++;
  y_step (ypos);  
  x_step (xpos);
  delay (SPEED);
  off_all() ;
}

void left_step (){
  xpos--;
  y_step (ypos);  
  x_step (xpos);
  delay (SPEED);
  off_all() ;  
}


void down_step ()
{
  ypos--;
  y_step (ypos);  
  x_step (xpos);
  delay (SPEED);
  off_all() ;
}

void up_step ()
{
  ypos++;
  y_step (ypos);  
  x_step (xpos);
  delay (SPEED);
  off_all() ;
}

void off_all ()
{
  digitalWrite(X1, LOW);
  digitalWrite(X2, LOW);
  digitalWrite(X3, LOW);  
  digitalWrite(Y1, LOW);
  digitalWrite(Y2, LOW);
  digitalWrite(Y3, LOW);

}

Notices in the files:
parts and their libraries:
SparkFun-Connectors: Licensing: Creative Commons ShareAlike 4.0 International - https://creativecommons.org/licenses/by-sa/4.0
